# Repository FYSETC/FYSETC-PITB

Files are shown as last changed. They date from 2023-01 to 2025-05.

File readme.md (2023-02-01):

## FYSETC PITB

### 1. Product introduction

Thanks for the great effort of the PCB designers [DFH](https://github.com/deepfriedheroin), [Armchair-Engineering](https://github.com/Armchair-Engineering), [kageurufu](Https://GitHub.com/kageurufu) and the other members from community to make this come true.

### 2. Hardware guide

#### 2.1 pinout

<table>
   <tr><td>Features</td><td>PITB Pin</td><td>RP2040 Pin</td><td>Pin No.</td><td>Comment</td></tr>
   <tr><td rowspan="4">X-MOTOR(1)</td><td>X-Step</td><td>GPIO8</td><td>11</td><td></td></tr>
   <tr><td>X-DIR</td><td>GPIO7</td><td>9</td><td></td></tr>
   <tr><td>X-EN</td><td>GPIO5</td><td>7</td><td></td></tr>
   <tr><td>X-CS/PDN</td><td>GPIO6</td><td>8</td><td></td></tr>
   <tr><td rowspan="4">Y-MOTOR(2)</td><td>Y-Step</td><td>GPIO12</td><td>15</td><td></td></tr>
   <tr><td>Y-DIR</td><td>GPIO11</td><td>14</td><td></td></tr>
   <tr><td>Y-EN</td><td>GPIO9</td><td>12</td><td></td></tr>
   <tr><td>Y-CS/PDN</td><td>GPIO10</td><td>13</td><td></td></tr>
   <tr><td rowspan="3">TMC Driver SPI </td><td>MOSI</td><td>GPIO3</td><td>5</td><td></td></tr>
   <tr><td>MISO</td><td>GPIO0</td><td>2</td><td></td></tr>
   <tr><td>SCK</td><td>GPIO2</td><td>4</td><td></td></tr>
   <tr><td rowspan="2">End-stops</td><td>X-STOP</td><td>GPIO23</td><td>35</td><td>Jumper connection for X-DIAG</td></tr>
   <tr><td>Y-STOP</td><td>GPIO24</td><td>36</td><td>Jumper connection for Y-DIAG</td></tr>
   <tr><td rowspan="3">FAN/RGB</td><td>FAN0</td><td>GPIO20</td><td>31</td><td></td></tr>
   </td><td>FAN1</td><td>GPIO21</td><td>32</td><td></td></tr>
   </td><td>RGB</td><td>GPIO29</td><td>41</td><td></td></tr>
   <tr><td rowspan="1">Temperature</td><td>TE0（THERM0）</td><td>GPIO26</td><td>38</td><td>A 4.7kOhm 0.1% temperature sensor pull up resistor is used,PT1000 can be connected directly. For PT100, an amplifier board must be used.</td></tr>
   <tr><td rowspan="2">CAN</td><td>TX</td><td>GPIO13</td><td>16</td><td></td></tr>
   <tr><td>RX</td><td>GPIO14</td><td>17</td><td></td></tr>
   <tr><td rowspan="2">EEPROM I2C Pin-Out</td><td>SCL</td><td>GPIO17</td><td>28</td><td></td></tr>
   <tr><td>SDA</td><td>GPIO16</td><td>27</td><td></td></tr>
   <tr><td rowspan="3">SWD Debug</td><td>SWDIO</td><td>SWDIO</td><td>25</td><td>only used for debugging now and can be used for other purposes.</td></tr>
   <tr><td>SWCLK</td><td>SWCLK</td><td>24</td><td>only used for debugging now and can be used for other purposes.</td></tr>
   </td><td>RESET</td><td>#RUN</td><td>26</td><td></td></tr>
</table>

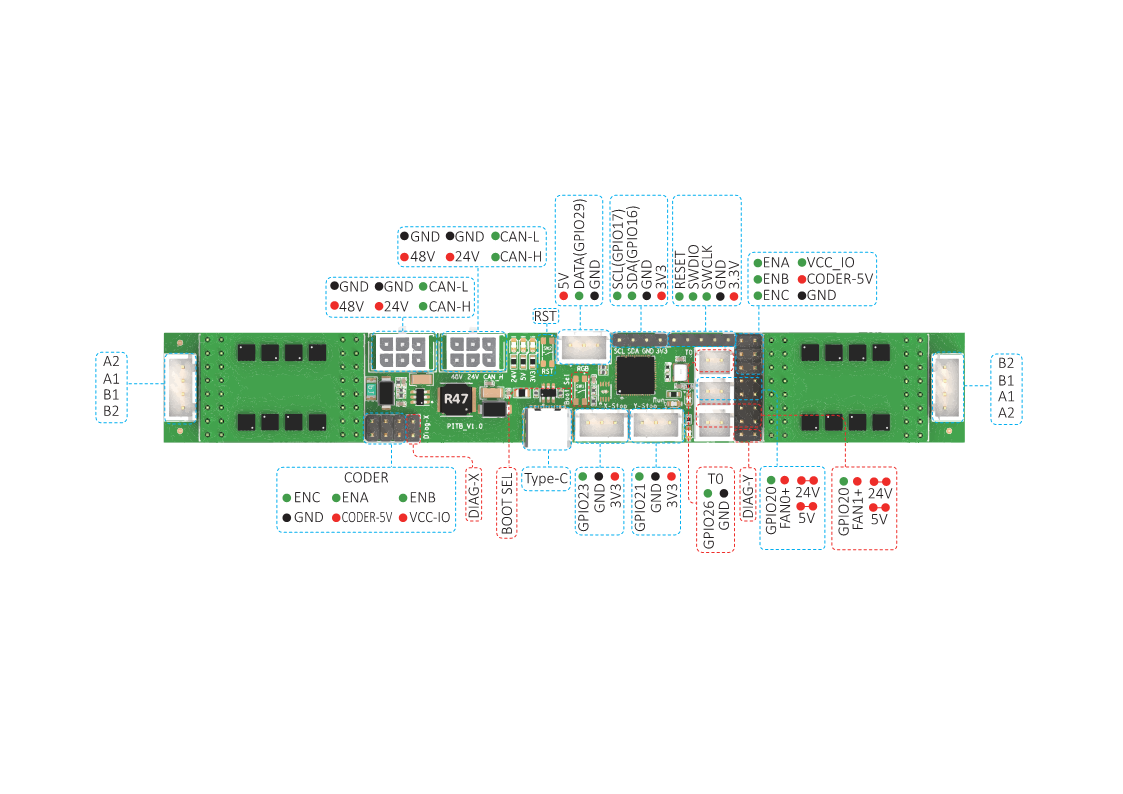
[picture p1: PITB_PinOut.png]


## Firmware

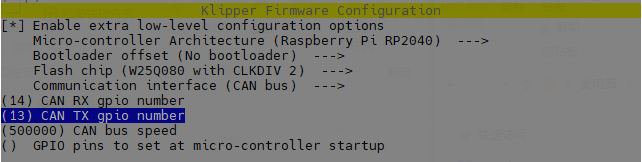
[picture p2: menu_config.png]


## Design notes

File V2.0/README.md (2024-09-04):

## PITB V2.0

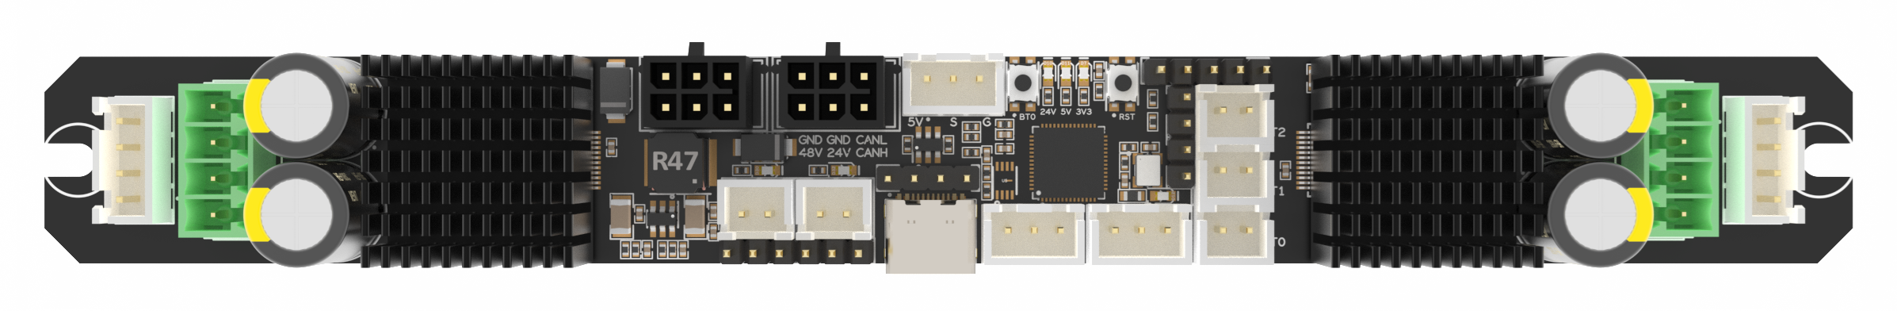
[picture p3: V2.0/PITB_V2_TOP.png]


### 1. Product introduction

Thanks for the great effort of the PCB designers [DFH](https://github.com/deepfriedheroin), [Armchair-Engineering](https://github.com/Armchair-Engineering), [kageurufu](Https://GitHub.com/kageurufu) and the other members from community to make this come true.

### 2. Hardware guide

#### 2.1 pinout

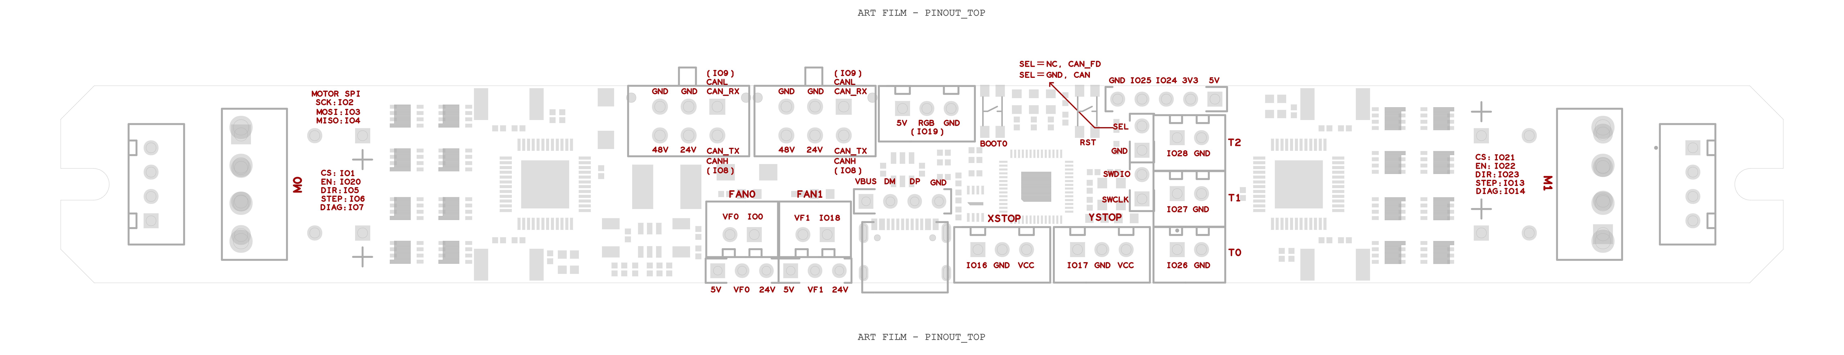
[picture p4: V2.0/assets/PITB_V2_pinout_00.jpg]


## Firmware

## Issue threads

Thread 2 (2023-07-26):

Unable to write tmc spi 'stepper_x' register GLOBALSCALER  HELPPP!!!

rbentoski2113, 2023-07-26:
I got the Fystec PITB with the 2 BIG 5160s can board, got it working on can and everything works, fans rgb  leds and whatnot but get this eror message when trying to move the x or y (what im using them on) steppers, googling has been of no help.   im still trying to rap my head around the spi/ ic2 bus and how it works, but has anyone else ran into this issue?

TekuSP, 2023-08-19:
You have to power 48V as well. Just jump 24V to both 48V and 24V rails.

rbentoski2113, 2023-08-19:
thank you! i thought i had updated this post i found this same coment somewhere like 20 mins after posting this orginaly.   If i may ask where did you find this out? cause there documentation is garbage

TekuSP, 2023-08-20:
By fucking around with wires until it started working.
At least now I can use thick 48V wires to transfer power to extruder CAN Board rather than thin 24 V wires...

ejhoness, 2024-08-31:
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

KoiosLabs, 2024-09-10:
Got the spi bus working: https://github.com/Klipper3d/klipper/pull/6683

ejhoness, 2024-09-20:
my pitbv2 is broken,

thanks, long life and prosperity.

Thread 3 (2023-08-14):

CODER pins not explained

TekuSP, 2023-08-14:
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
For what purpose are used those pins? What should be connected to them? ABZ from Encoder? Do they lead to ABN in TMC?

rbentoski2113, 2023-08-24:
i second this

> 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 For what purpose are used those pins? What should be connected to them? ABZ from Encoder? Do they lead to ABN in TMC?

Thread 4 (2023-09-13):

What model are the two 6-pin connectors for the CAN-BUS

abassign, 2023-09-13:
What model are the two 6-pin connectors for the CAN-BUS and voltages 24 and 48? Is it possible to find them on Amazon?

rbricheno, 2023-09-19:
I have one of these boards in hand and measured the connectors to work this out.

They are  "43025-0600" 6 circuit Micro-fit 3.0 connectors as described here: https://www.utmel.com/components/43025-0800-micro-fit-3-0-receptacle-housing-dual-row-drawing-datasheet-and-equivalents?id=1277

I took a photograph of the board next to some calipers which you can see here:  https://imgur.com/a/ZejbaVU

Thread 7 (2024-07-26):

PIN description for V2 is just a copy of that for V1. Couod you please correct it? Thanks.

salbang, 2024-07-26:

eddwatts, 2024-07-27:
been working on this myself and have put in a pull request to it, pinouts, sample cfg and firmware details for klipper
[https://github.com/eddwatts/FYSETC-PITB/tree/main/V2.0](https://github.com/eddwatts/FYSETC-PITB/tree/main/V2.0
)
Only bit untested are the SPI ports as im not sure there working on my board, everything else is right and according to the schematics they should work so please try and give feedback

salbang, 2024-07-28:
@eddwatts Thanks. Will try it once I get the v2 one delivered.

ejhoness, 2024-08-31:
for me, at the moment, spi errors, tmc dump only ffffffffff, and not working fan0 fan1 temp port012 ok and sensor GPIO29_ADC3 ok
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

:(

KoiosLabs, 2024-09-10:
Got the spi bus working: https://github.com/Klipper3d/klipper/pull/6683

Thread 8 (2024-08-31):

support PITbv2

ejhoness, 2024-08-31:
I'm sad about this, please show me a video of this working with klipper. A simple motor rotating connected to this. PITBv2. and the files used to run this motor.

ejhoness, 2024-09-06:
Thanks for the update, but only temperature and end of stroke sensor. No motor and fans

[klippy_pitbv2.log](https://github.com/user-attachments/files/16910681/klippy_pitbv2.log)
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

KoiosLabs, 2024-09-10:
Got the spi bus working: https://github.com/Klipper3d/klipper/pull/6683

ejhoness, 2024-09-20:
my pitbv2 is broken,
thanks, long life and prosperity.

Closed 2024-09-20.

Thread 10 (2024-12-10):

PITB board not recognized by CAN network, tool head board in passthrough works fine.

LadPack, 2024-12-10:
I am trying and failing to have the Party in the back (PITB) board recognized.

I know the CAN wiring is correct, because I have it daisy chained with a toolhead board (downstream of the PITB) that is running fine on klipper, it's just the PITB board that isn't running

I'm using these settings https://github.com/kageurufu/PITB/tree/main/firmware
I am able to see the board over USB, but once I put it into the CAN network I see just the toolhead board like below.

I have also double triple checked the wiring on the board and made sure it is getting the appropriate power.

I am following esotericals guide online, including all of the steps for troubleshooting no UUID, I have reinstalled the katapult software multiple times, each time it appears to install normally.

FWIW, I did have to take down the CAN network and then bring it back up with 1m and qlen 1024, and that worked for the toolhead board (ebb36) that I was able to successfully install klipper on.

I have also removed the ebb36 from the loop, and am now just trying to flash the PITB on it's own. I have also tried with and without the CAN FD Jumper

LadPack, 2024-12-11:
closing, pins were incorrectly labelled on pictures

NAPCAL, 2025-03-19:
Your issue might just be this https://github.com/FYSETC/FYSETC-PITB/issues/11

NAPCAL, 2025-03-19:
The V1.0 has the identical CAN bus termination resistors installed, so your issue is the same as the V2.0. The PITB can only be used as an end of the bus device since termination has to be at the ends of the bus. https://github.com/FYSETC/FYSETC-PITB/issues/11

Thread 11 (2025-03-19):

PITB V2 bad CAN bus design with pass through connector with on-board bus termination (R28 & R29)

NAPCAL, 2025-03-19:
With R28 & R29 installed and no jumpers to disconnect them from the CAN bus, this board will only work as an end of the CAN bus device, and the additional connector is only suitable for passing power onto other devices.

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

Currently, these two resistors are tiny SMD; it will be almost impossible for a hobbyist to remove them without damaging the board.

I wanted to use the pass-through connector to supply the +24V, GND, CAN_L, & CAN_H onto my BTT SB2240 tool headboard, with it being the last device on the bus.

Jawfish1024, 2025-03-20:
I was able to use the flash the PITB as a USB can bus bridge to control my EBB 42 and Cartographer so it is the 1st device on the bus.
I still had to connect the board via USB from my Pi though

erdoganguner2004-code, 2025-09-05:
So, in order to use the second port for pass-through, is the solution as simple as removing the resistor?

NAPCAL, 2025-09-05:
Yes, both resistors are the most miniature SMD resistors I have seen.

Kapton tape to protect the other parts around the resistors, a heat gun (like Weller 6966C) or SMD rework gun, and a very small set of tweezers.

Weller 6966C is a very old product and maybe discontinued, but it keeps working and working.

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

NAPCAL, 2025-09-06:
CAN bus has very specific physical layer requirements to prevent noise and ringing during communications.

Bench setups (Bench testing) typically will not recreate bus wires running past wiring that can induce noise into the bus, nor will they recreate the movement of the bus wires for tool head boards.

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

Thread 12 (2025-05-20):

Homing wrong direction.

raschinger, 2025-05-20:
The default config file is nearly unusable. Therefore I used the fork from eddwatts. But still unusable. Could you please double check the pinout and so on?

It basically homed in the wrong direction. Steppers movement aren't invented confirmed it with force move in positiv direction.

https://github.com/user-attachments/assets/319c0959-71ea-45f4-a731-72db970b7530

[stepper_x]
step_pin = PITB:gpio6
dir_pin = !PITB:gpio5
enable_pin = !PITB:gpio20
endstop_pin = tmc5160_stepper_x:virtual_endstop
homing_retract_dist = 20
rotation_distance = 40
position_min = 0
position_endstop = 250
position_max = 250
homing_positive_dir = true
homing_speed = 150.0
second_homing_speed = 10.0
microsteps = 32

[tmc5160 stepper_x]
spi_bus = spi0_gpio4_gpio3_gpio2
cs_pin = PITB:gpio1
diag1_pin = PITB:gpio7
driver_sgt = -64
interpolate = False
run_current = 1

[stepper_y]
step_pin = PITB:gpio13
dir_pin = !PITB:gpio23
enable_pin = !PITB:gpio22
endstop_pin = tmc5160_stepper_y:virtual_endstop
homing_retract_dist = 20
rotation_distance = 40
position_min = 0
position_endstop = 250
position_max = 250
homing_positive_dir = true
homing_speed = 150.0
second_homing_speed = 10.0
microsteps = 32

[tmc5160 stepper_y]
spi_bus = spi0_gpio4_gpio3_gpio2
cs_pin = PITB:gpio21
diag1_pin = PITB:gpio14
driver_sgt = -64
interpolate = False
run_current = 1

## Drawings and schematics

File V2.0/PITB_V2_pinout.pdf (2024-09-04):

# ART FILM - PINOUT_TOP

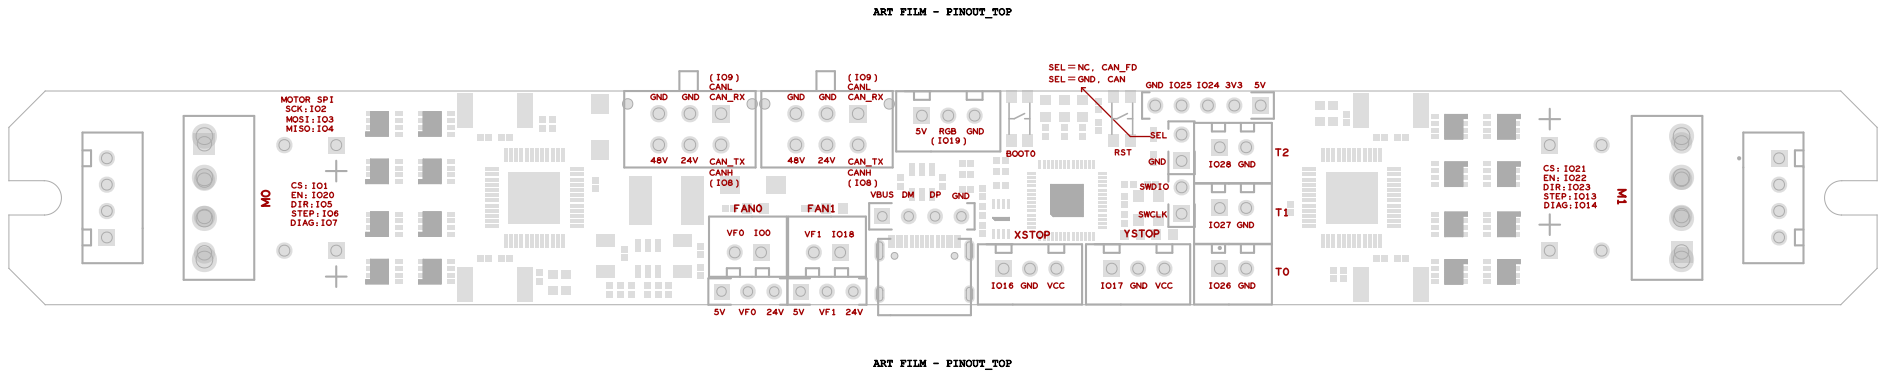
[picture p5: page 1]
ART FILM - PINOUT_TOP; SCK:IO2; MISO:IO4; MOSI:IO3; MOTOR SPI; DIAG:IO7; STEP:; DIR:; GND; CANH; CAN_TX; CANL; CAN_RX; FAN0; FAN1; VBUS; RGB; XSTOP; BOOT0; VCC; RST; YSTOP; SWCLK; SWDIO; SEL; DIAG:IO14; STEP:IO13

SEL NC, CAN_FD
SEL GND, CAN

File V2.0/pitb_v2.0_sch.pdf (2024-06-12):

5

4

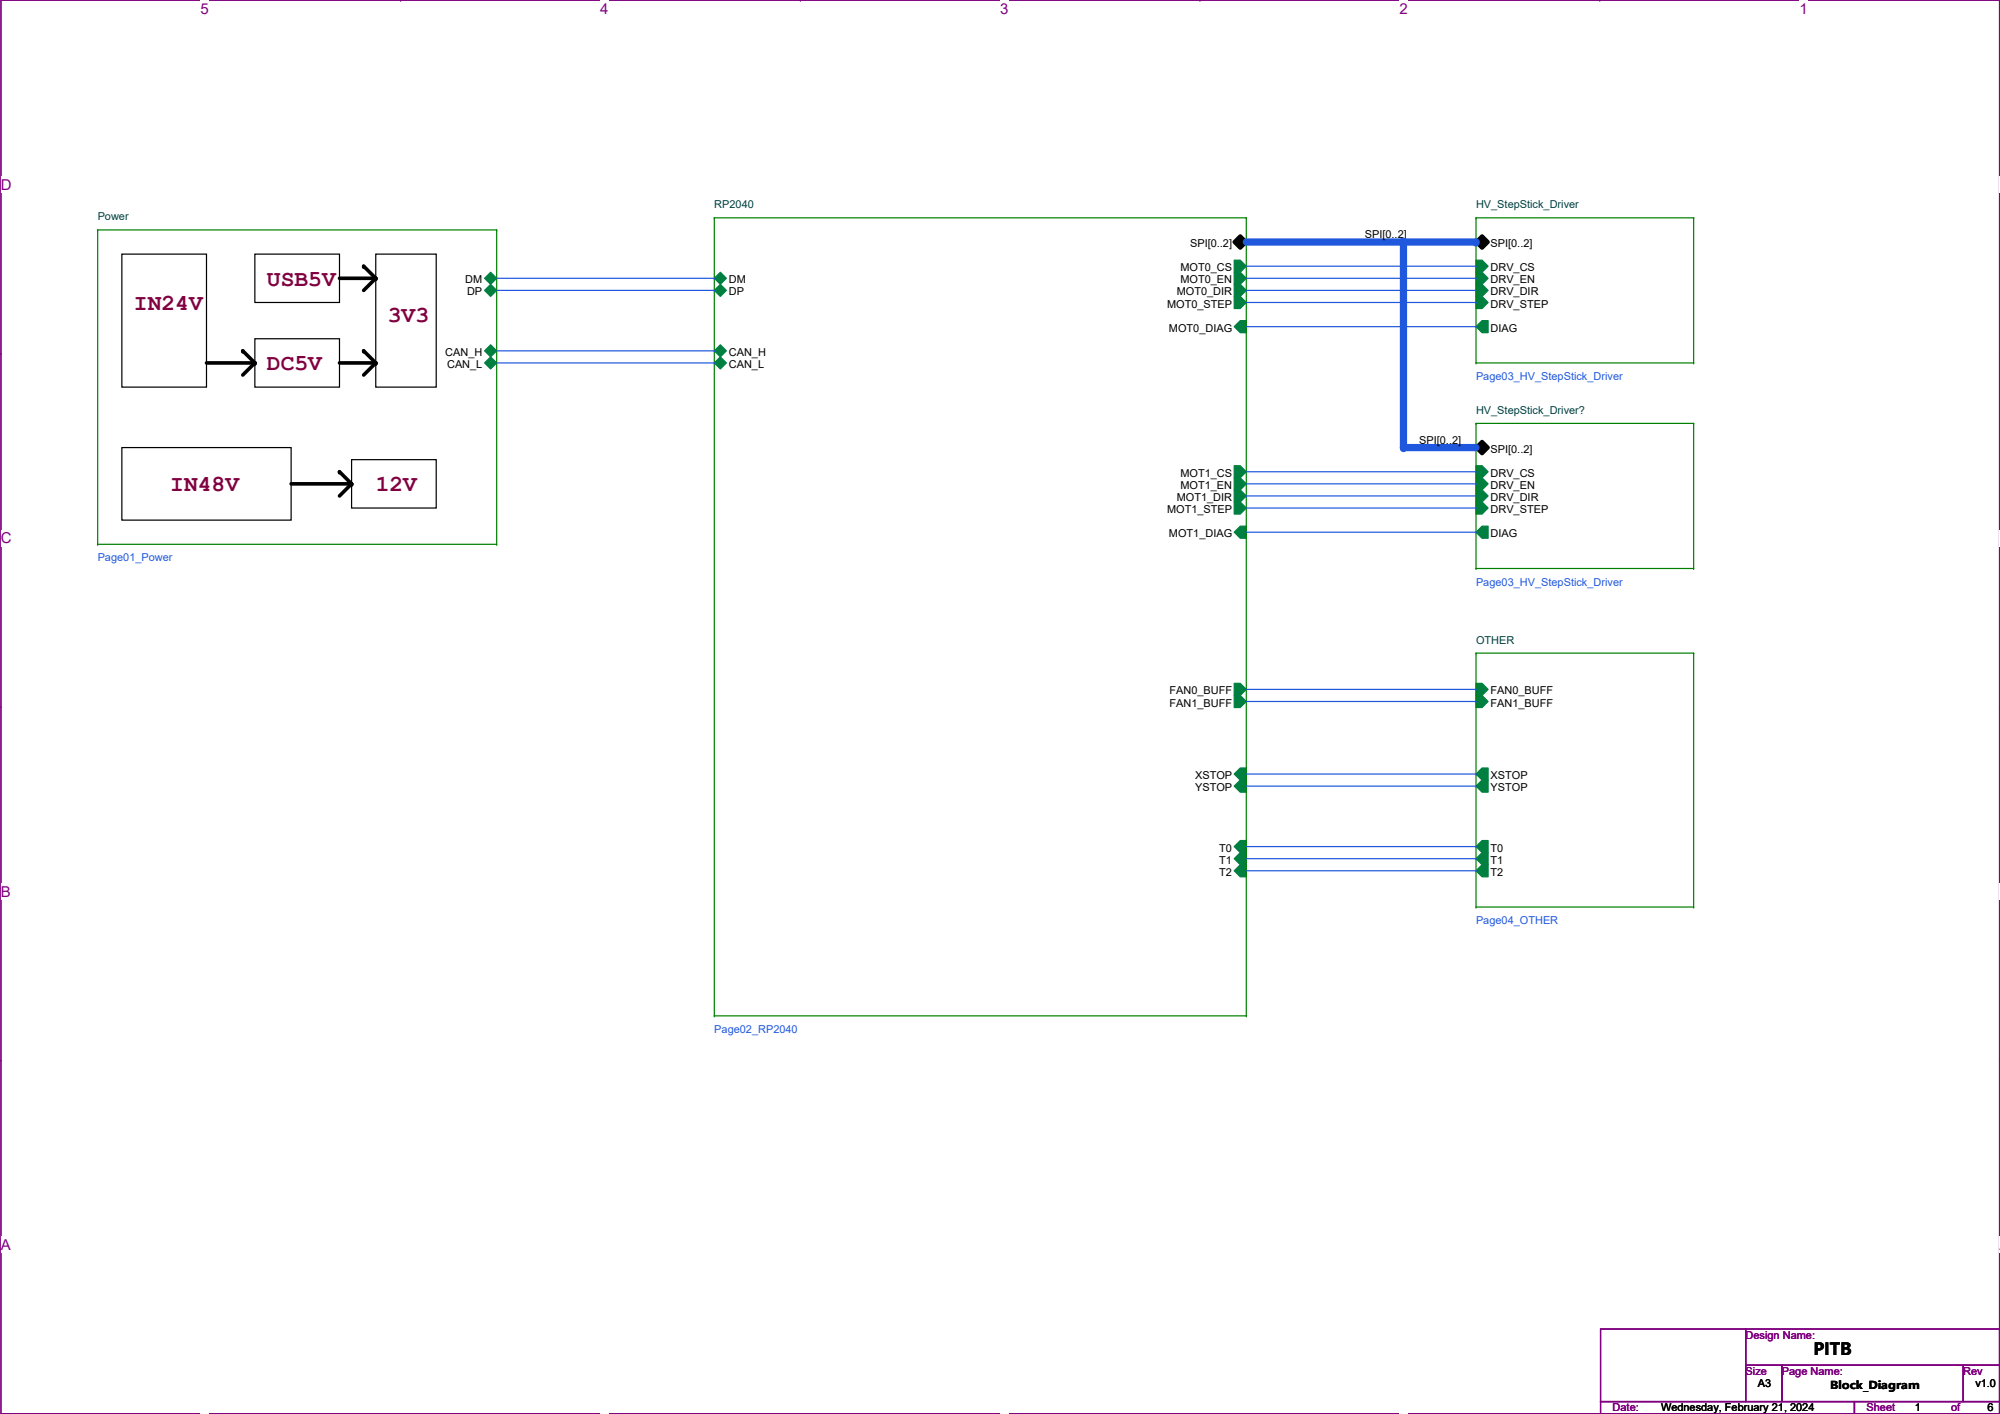
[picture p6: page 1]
USB5V; Design Name:; Size; Page Name:; Rev; Date:; Sheet; PITB; Wednesday, February 21, 2024; Block_Diagram; Page02_RP2040; MOT1_EN; FAN0_BUFF FAN1_BUFF; SPI[0..2]; MOT1_CS; MOT1_DIR MOT1_STEP; CAN_H CAN_L; YSTOP; XSTOP; MOT0_DIR; MOT0_EN; MOT0_DIAG; MOT0_STEP; MOT0_CS; MOT1_DIAG; HV_StepStick_Driver?; Page03_HV_StepStick_Driver; DIAG; DRV_DIR; DRV_EN; DRV_STEP; DRV_CS; HV_StepStick_Driver; OTHER; Page04_OTHER; XSTOP YSTOP; Power; Page01_Power

D D

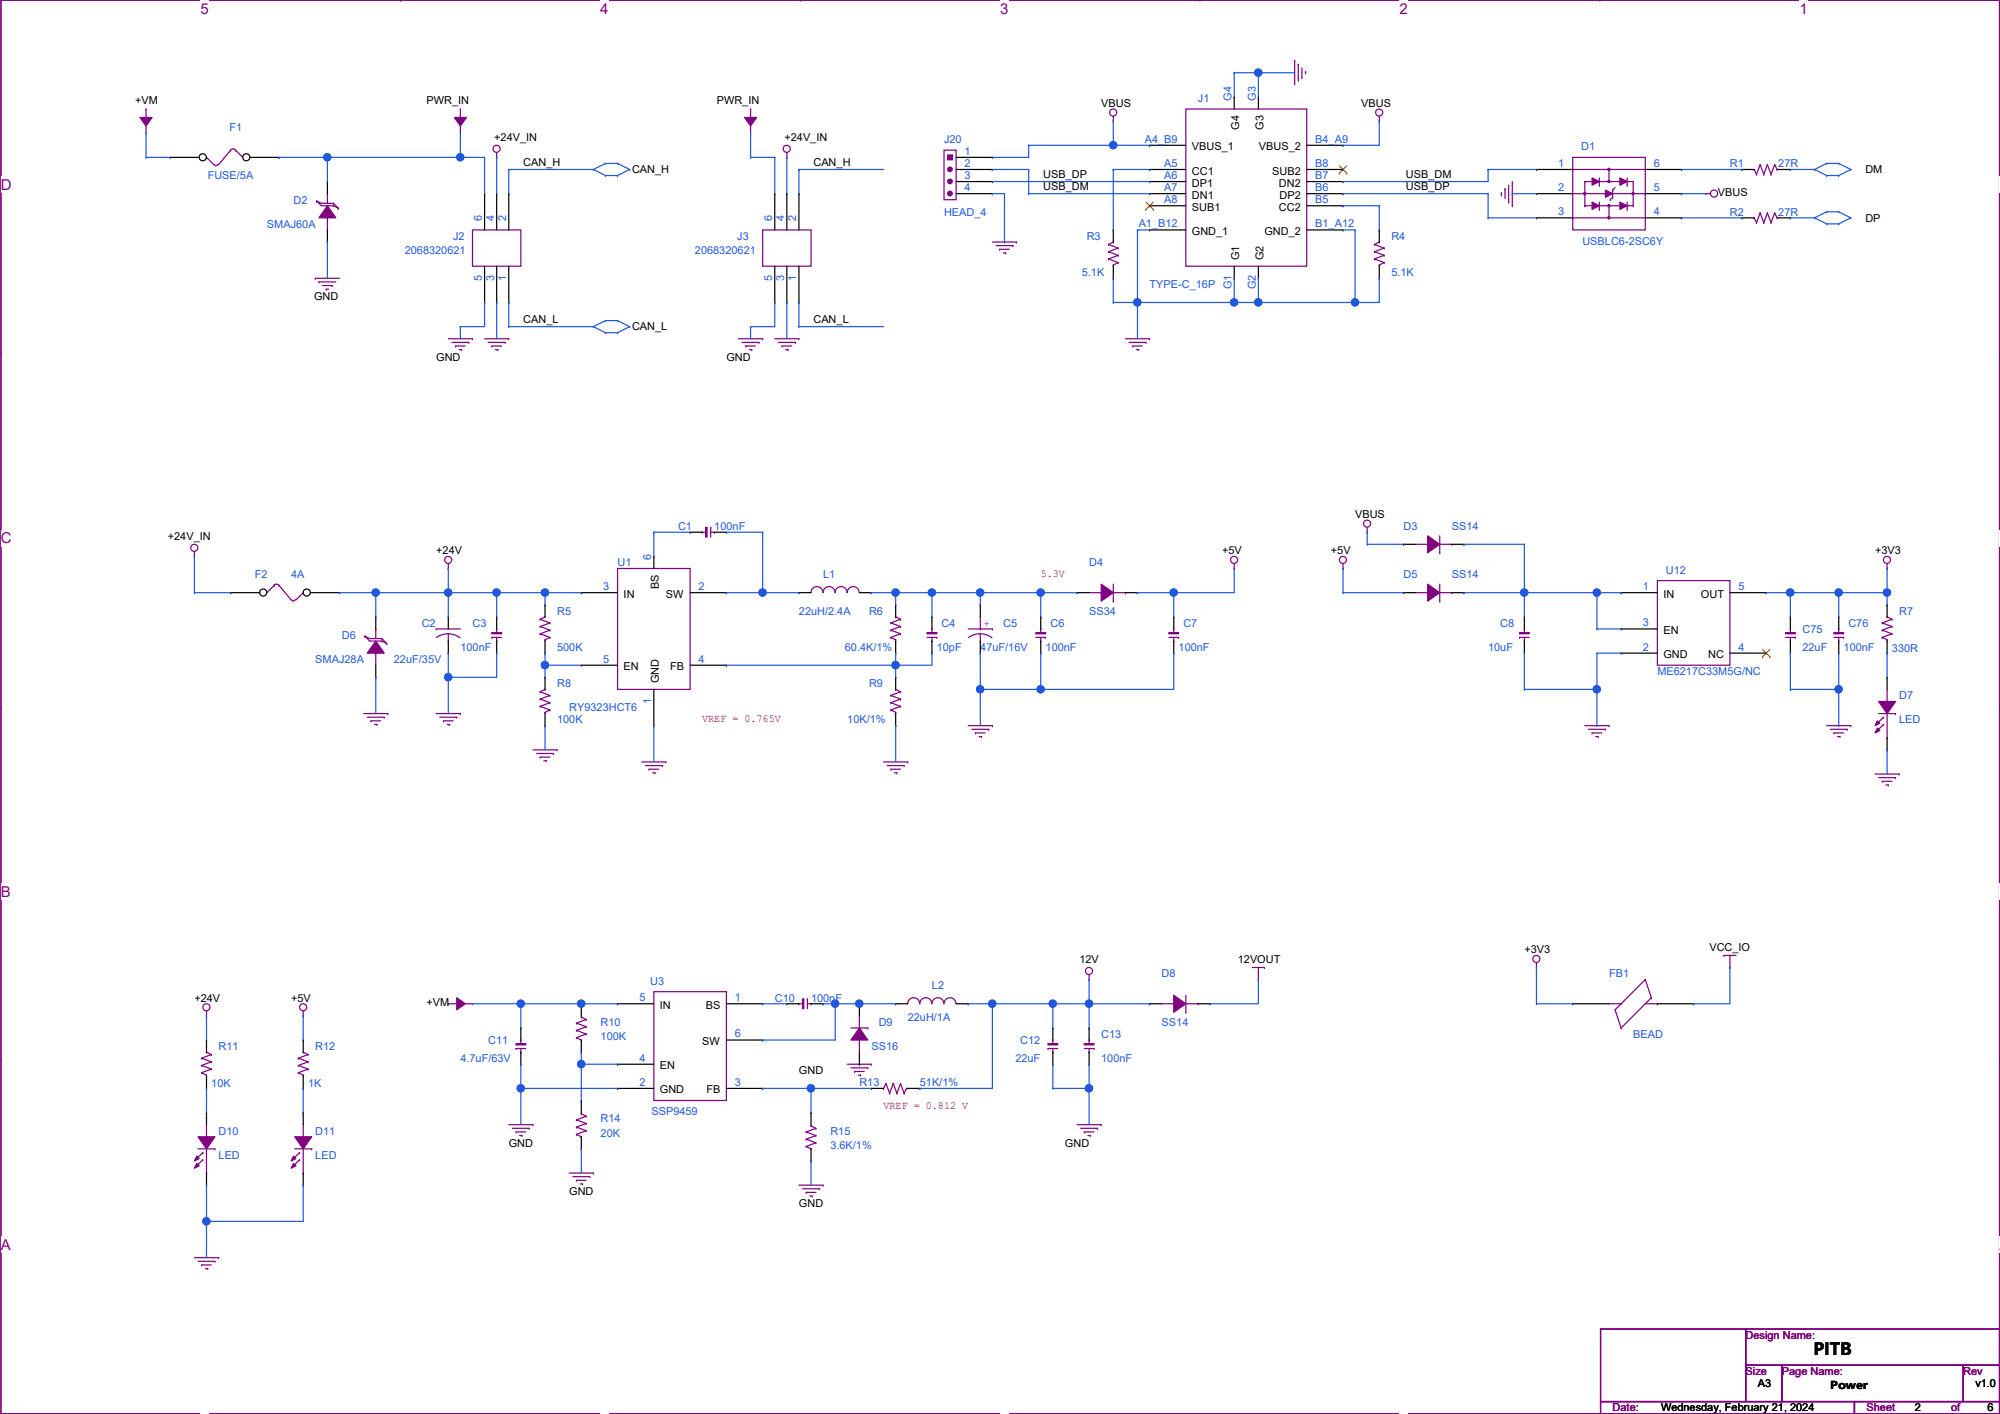
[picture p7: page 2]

D D

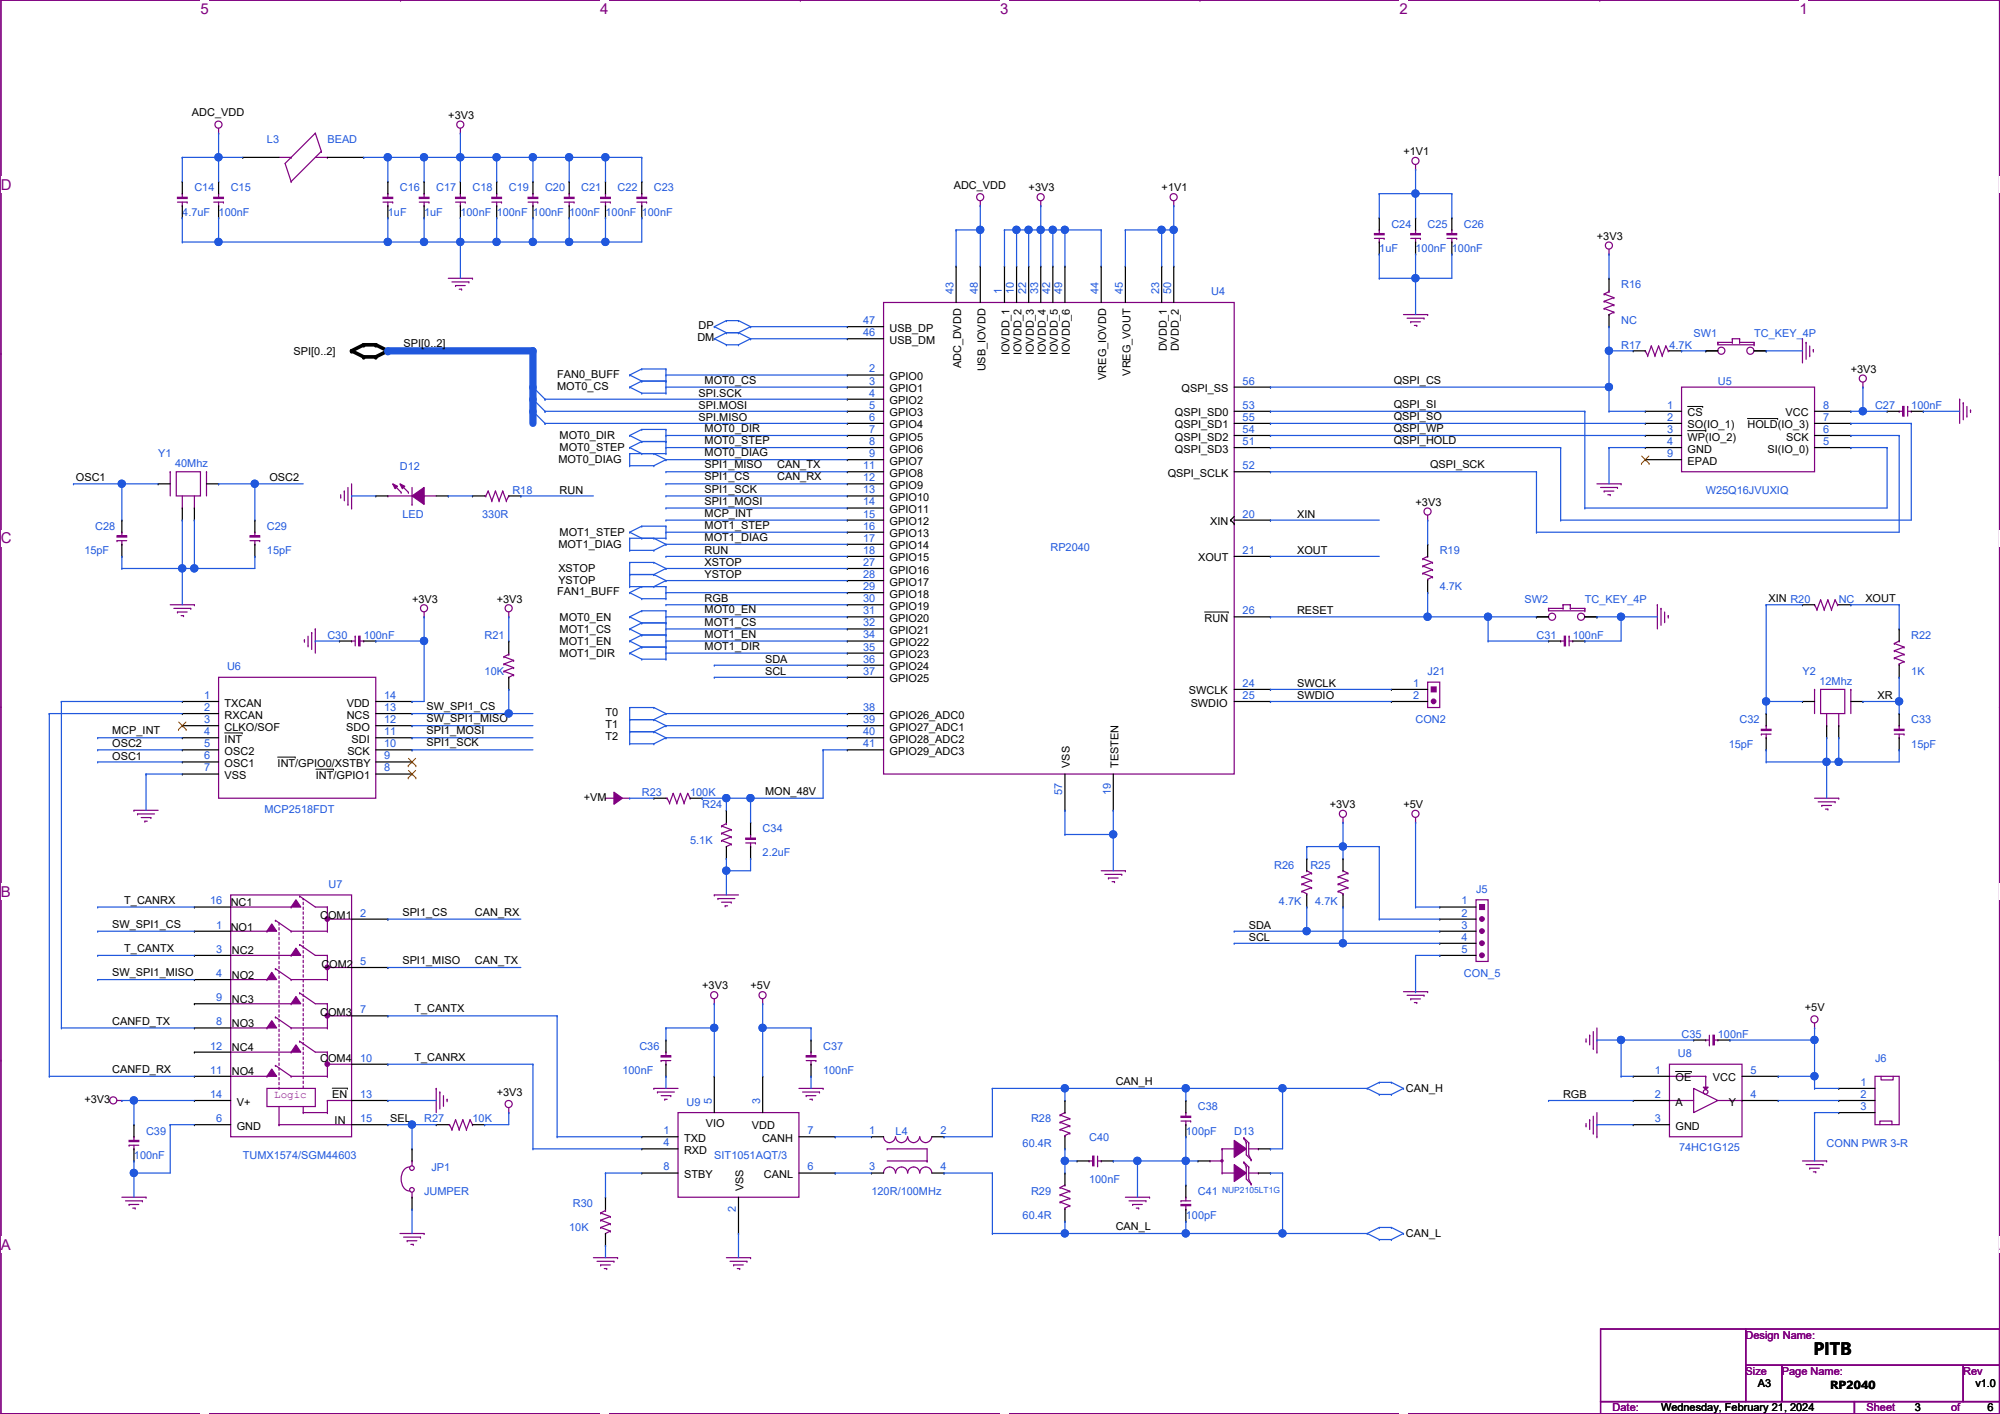
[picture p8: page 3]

D D

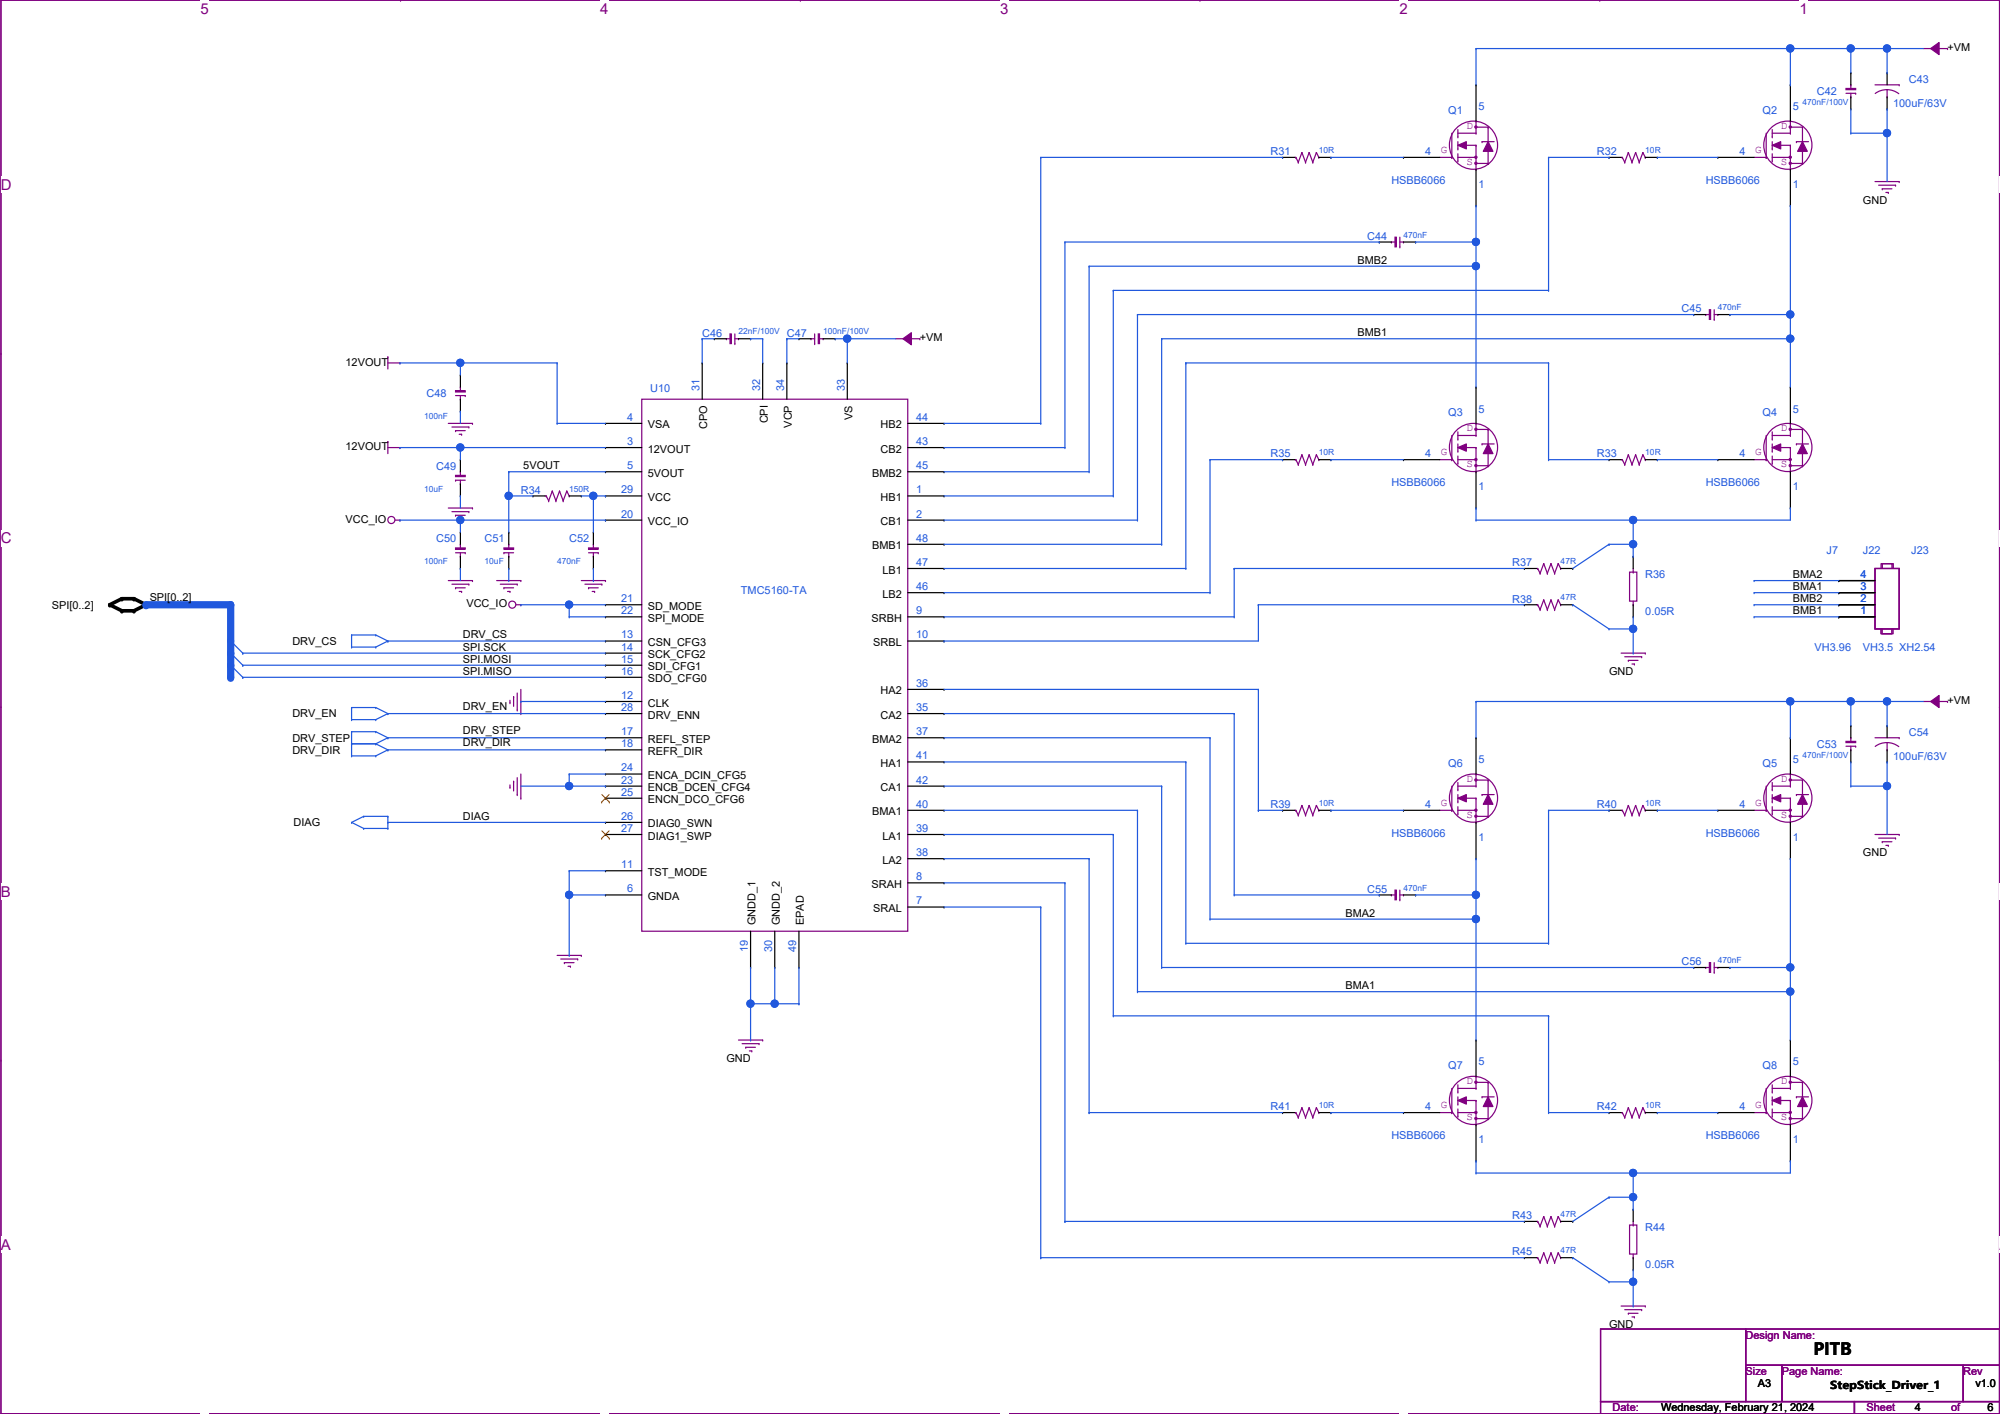
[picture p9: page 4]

D D

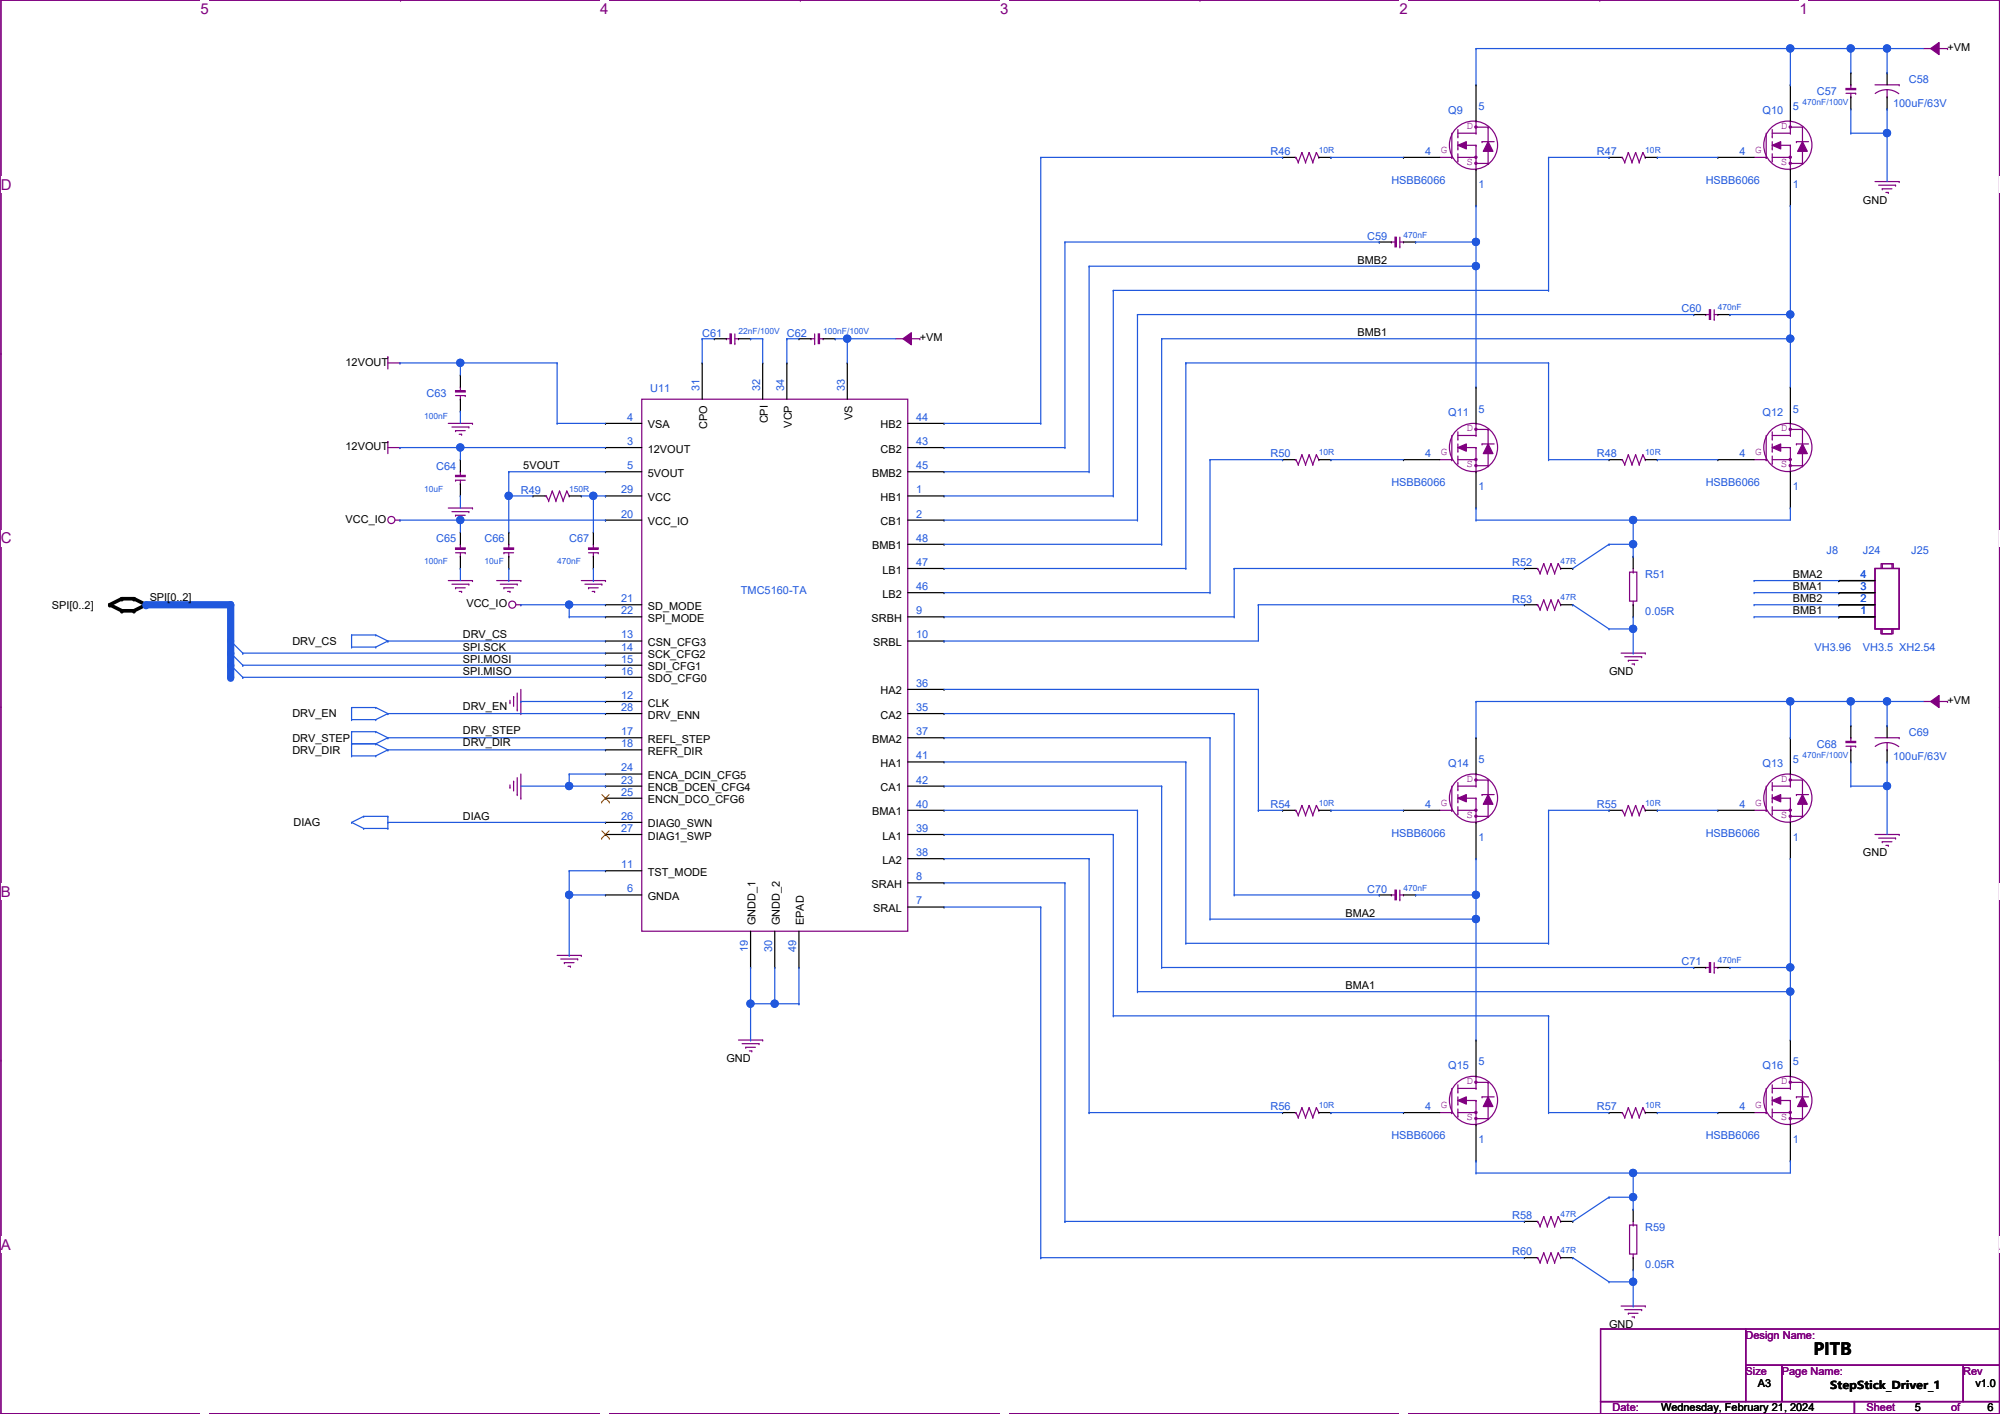
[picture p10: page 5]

D D

# Fan

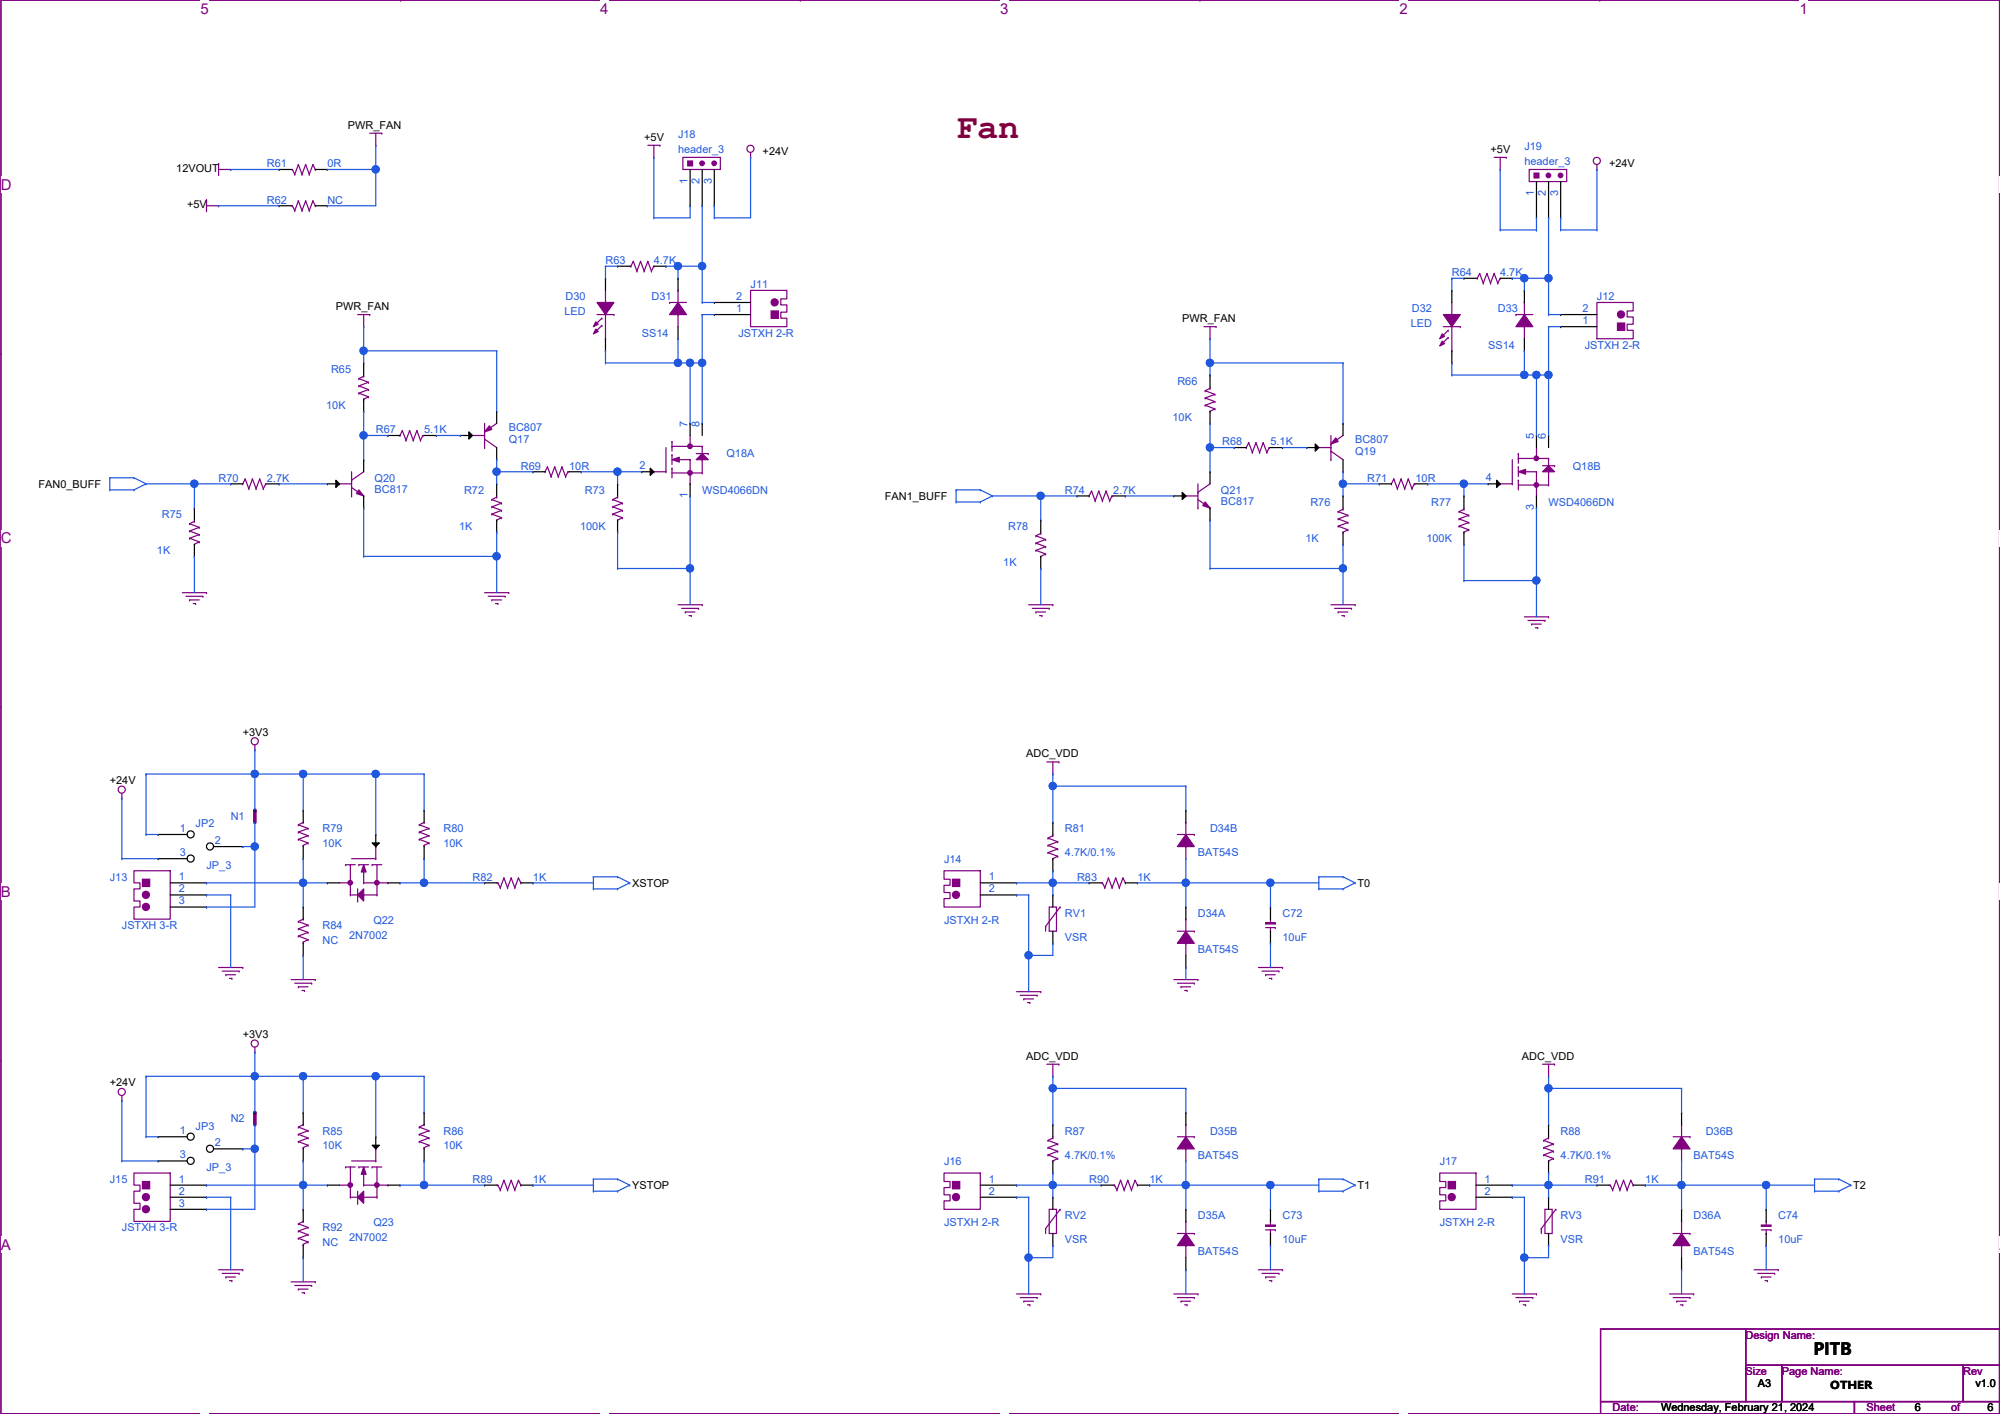
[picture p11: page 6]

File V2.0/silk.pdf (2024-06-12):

# ART FILM - adt

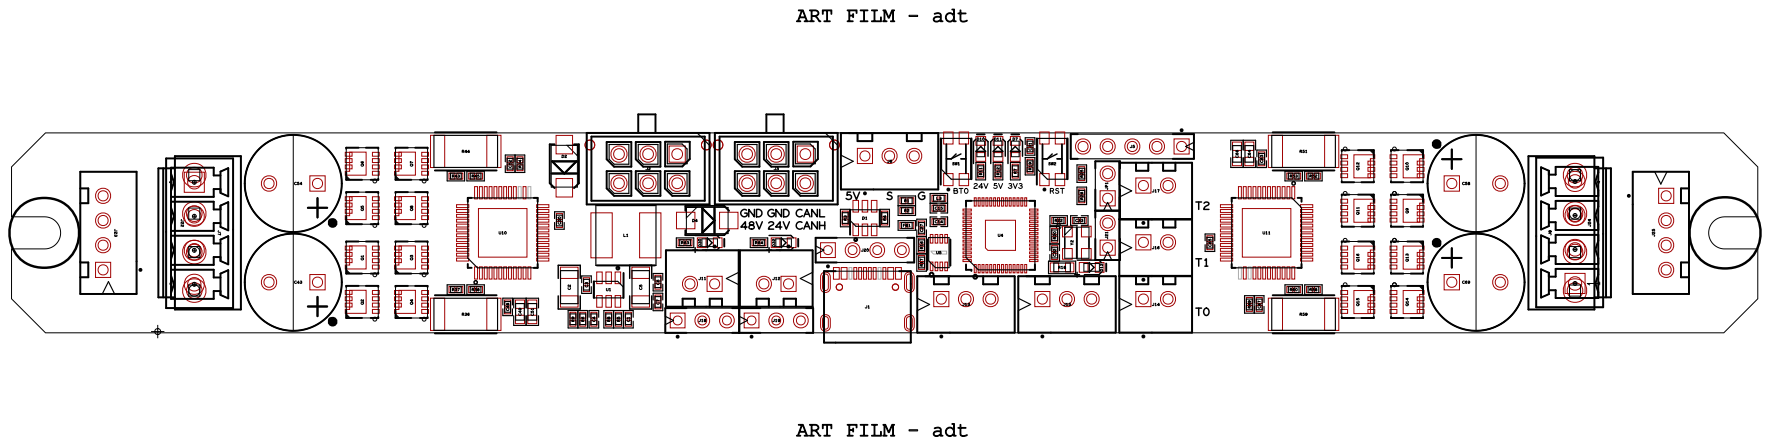
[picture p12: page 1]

# ART FILM - adb

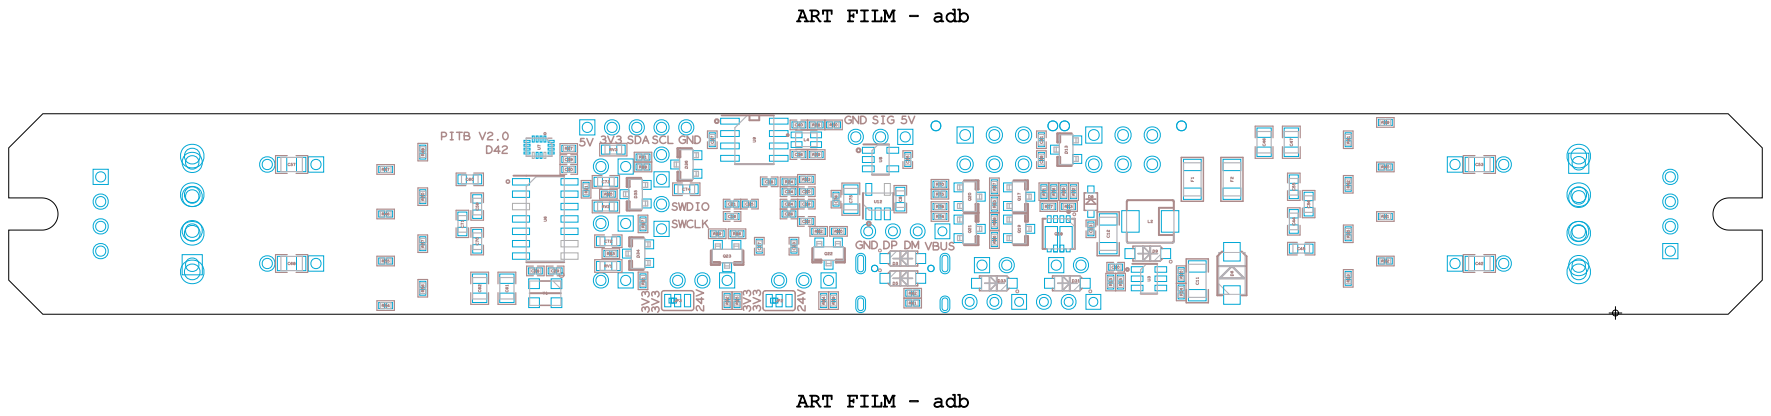
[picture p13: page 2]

# ART FILM - silktop

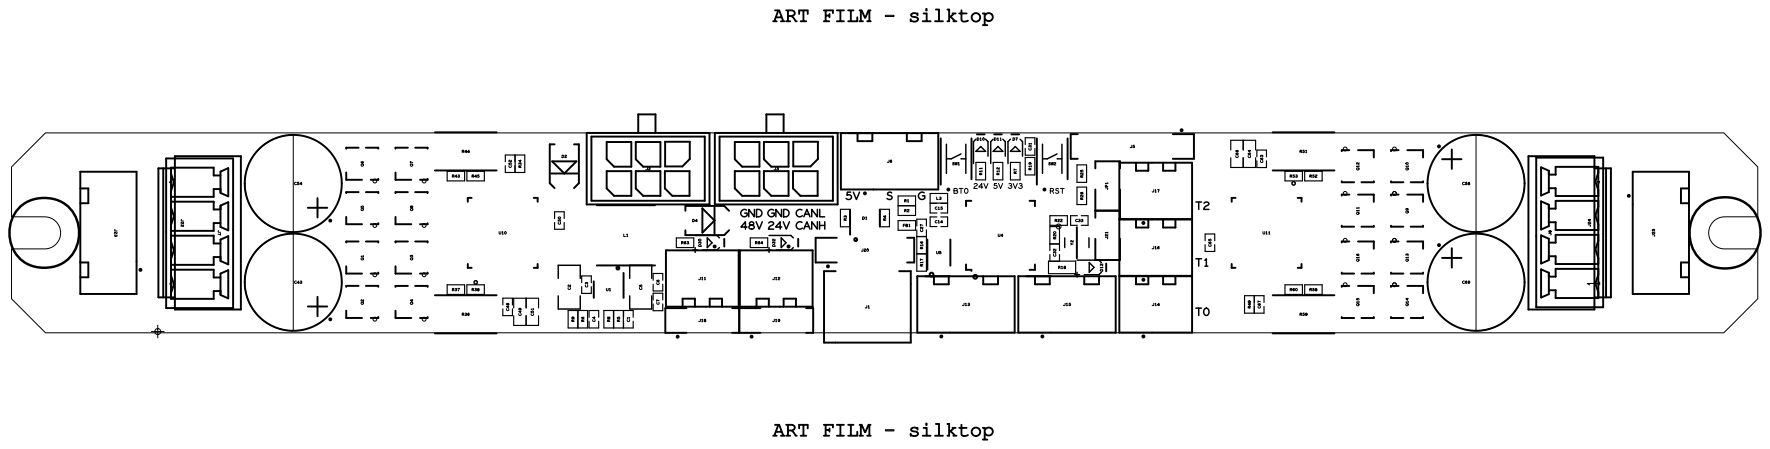
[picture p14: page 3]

# ART FILM - silkbotm

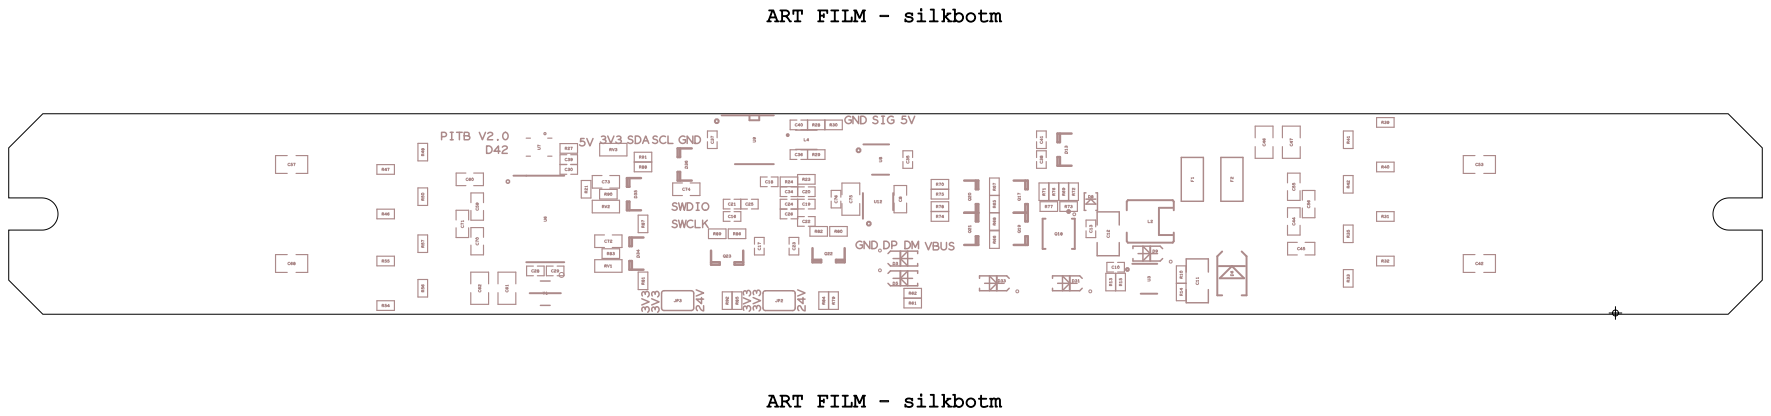
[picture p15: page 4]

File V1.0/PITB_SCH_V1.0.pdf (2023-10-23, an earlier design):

### IN24V

### USB5V

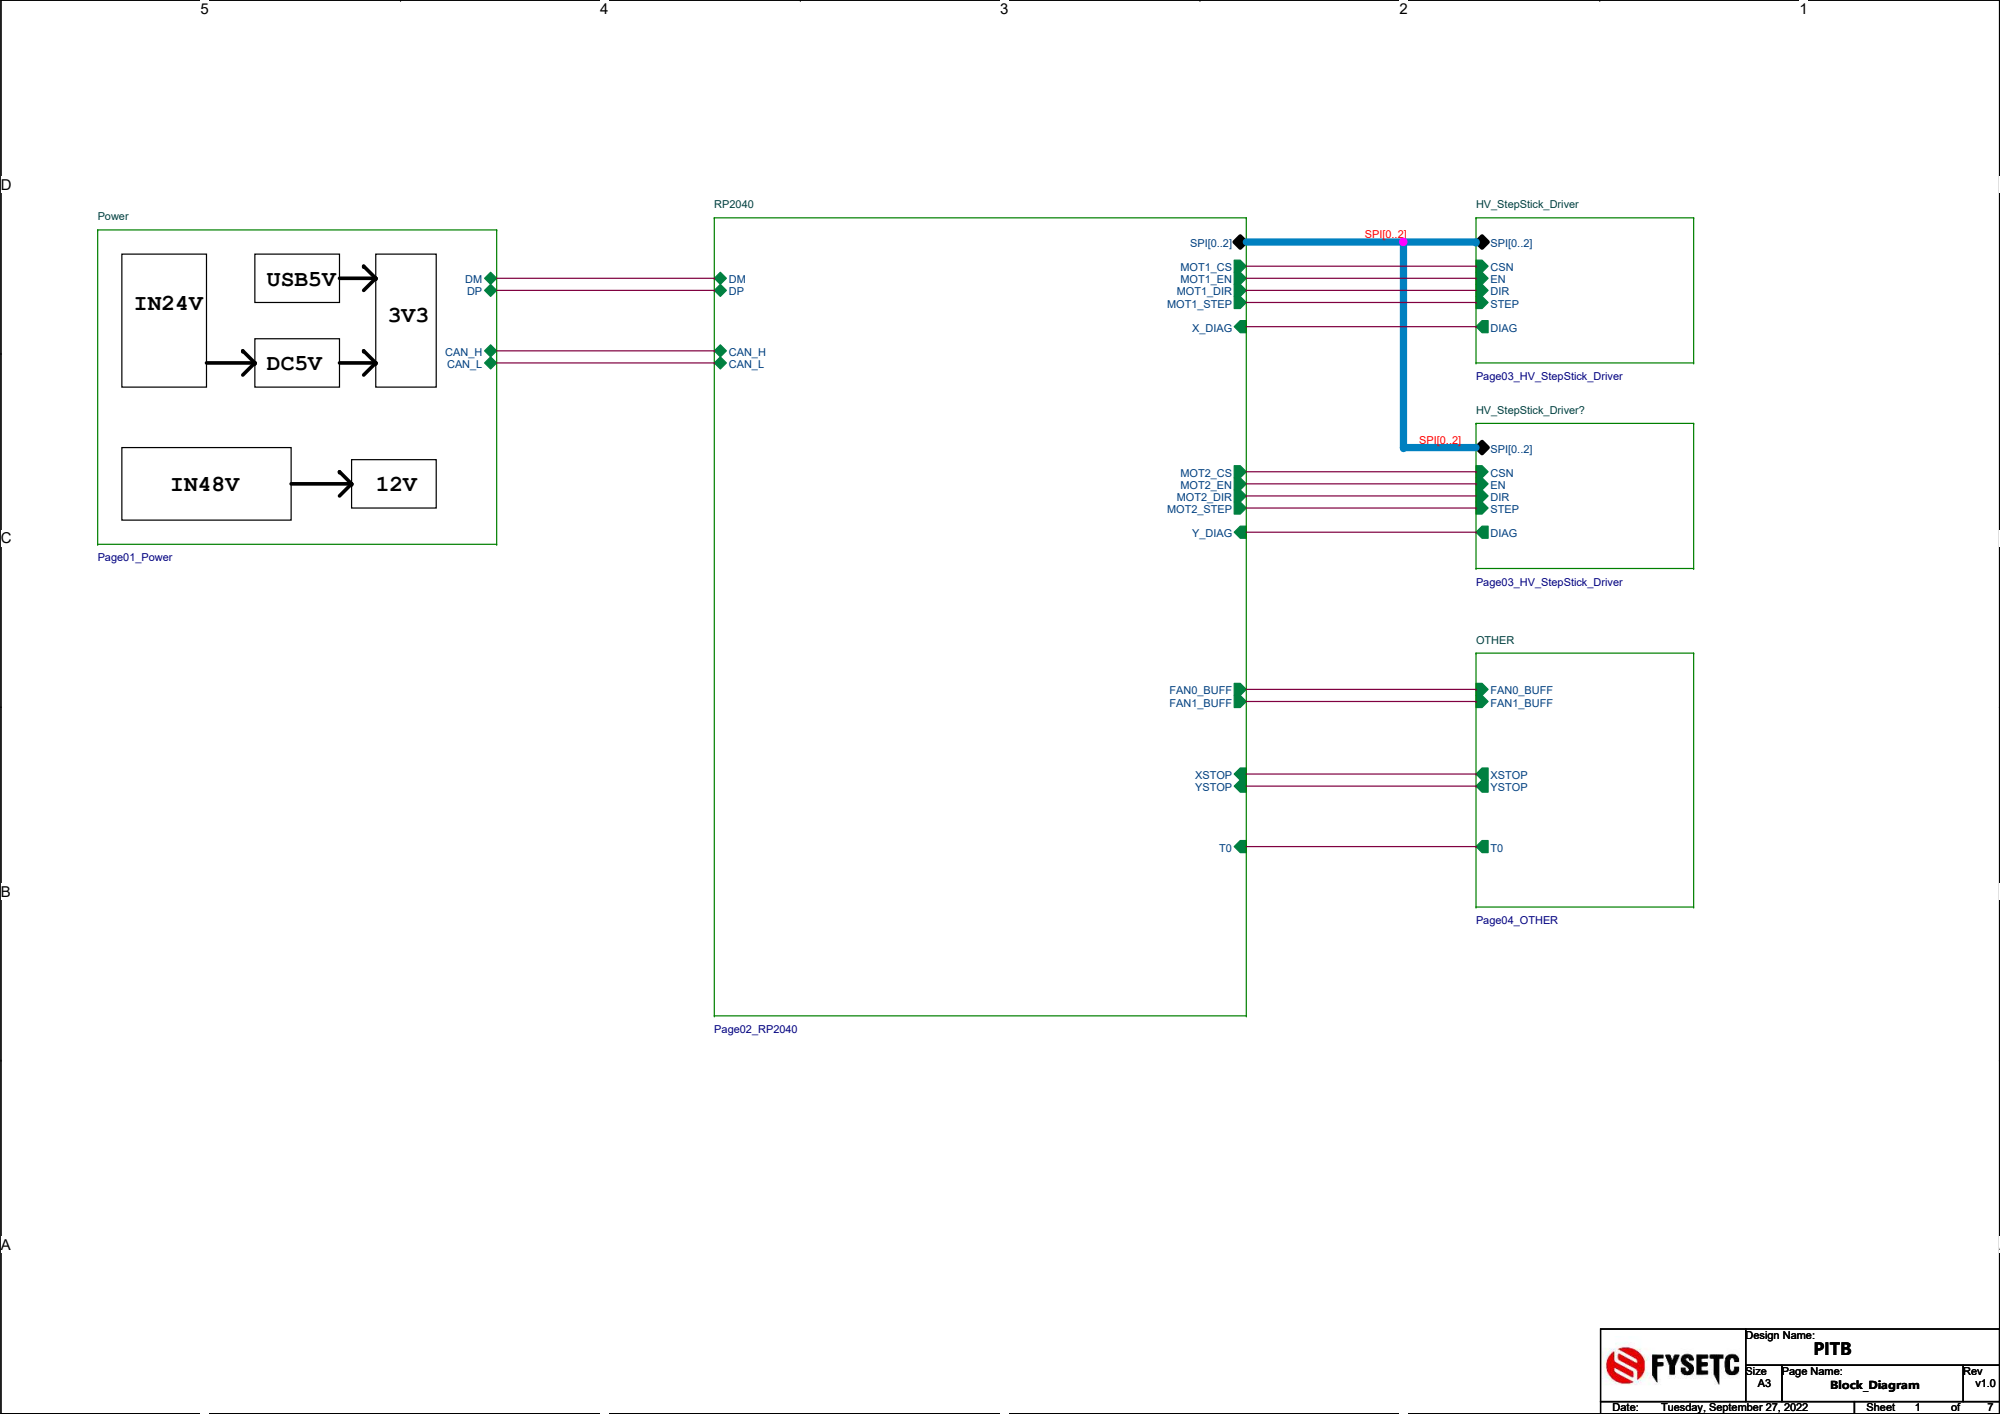
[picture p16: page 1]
Design Name:; Size; Page Name:; Rev; Date:; Sheet; PITB; Tuesday, September 27, 2022; Block_Diagram; Page02_RP2040; MOT1_EN; FAN0_BUFF FAN1_BUFF; SPI[0..2]; MOT1_CS; MOT1_DIR MOT1_STEP; MOT2_EN; MOT2_CS; MOT2_DIR MOT2_STEP; CAN_H CAN_L; X_DIAG; YSTOP; XSTOP; Y_DIAG; HV_StepStick_Driver?; Page03_HV_StepStick_Driver; CSN; DIR STEP; DIAG; HV_StepStick_Driver; OTHER; Page04_OTHER; XSTOP YSTOP; Power; Page01_Power

5 | 4 | 3 | 2 | 1

D


PAGE1 PAGE1 PAGE1

Wednesday, September 14, 2022 Wednesday, September 14, 2022 Wednesday, September 14, 2022 | 2 2 2 7 7 7

D


Power Power Power

Wednesday, September 14, 2022 Wednesday, September 14, 2022 Wednesday, September 14, 2022 | 3 3 3 7 7 7

D


QSPI_SO | SO(IO_1) 2
QSPI_WP | WP(IO_2) 3

Wednesday, September 14, 2022 Wednesday, September 14, 2022 Wednesday, September 14, 2022 | 4 4 4 7 7 7

D


StepStick_Driver_1 StepStick_Driver_1 StepStick_Driver_1

Wednesday, September 14, 2022 Wednesday, September 14, 2022 Wednesday, September 14, 2022 | 5 5 5 7 7 7

D


StepStick_Driver_1 StepStick_Driver_1 StepStick_Driver_1

Wednesday, September 14, 2022 Wednesday, September 14, 2022 Wednesday, September 14, 2022 | 6 6 6 7 7 7

D

# Fan


OTHER OTHER OTHER

Wednesday, September 14, 2022 Wednesday, September 14, 2022 Wednesday, September 14, 2022 | 7 7 7

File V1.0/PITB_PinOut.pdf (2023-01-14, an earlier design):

CAN-H; GND CODER-5V; ENC ENA; DIAG-X; ENB; GPIO20 FAN0+; VCC-IO; RST; BOOT SEL; ENA ENB ENC; VCC_IO CODER-5V GND; GPIO26; GND; DATA(GPIO29); SCL(GPIO17); SDA(GPIO16); GND 3V3; RESET; SWDIO SWCLK GND 3.3V; Type-C; GPIO23; GPIO21; CODER; DIAG-Y; GPIO20; FAN1+24V 5V

GND GND CAN-L

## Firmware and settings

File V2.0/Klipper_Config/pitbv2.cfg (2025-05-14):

[mcu PITB]
##  You need to select 'Communication interface' to USB in 'make menuconfig'
##  when you compile Klipper
##	Obtain definition by "ls -l /dev/serial/by-id/" then unplug to verify
##--------------------------------------------------------------------
#serial: /dev/serial/by-id/usb-Klipper_rp2040_E66160F423669A37-if00
canbus_uuid=e3cfde1a684f
## When using klipper with PITB V2, you can only use CAN or USB. When using CAN, 
## you need to short-circuit SEL and GND, that is, plug in the jumper cap.
## Uncomment below if you're using the Raspberry uart0 to communicate with Spider
#restart_method: command

#####################################################################
#      X/Y Stepper Settings
#####################################################################

[stepper_x]
##	Connected to MOT0 (B Motor)
step_pin: PITB:gpio6
dir_pin: PITB:gpio5
enable_pin: !PITB:gpio20
rotation_distance: 40
microsteps: 16
full_steps_per_rotation:200  #set to 400 for 0.9 degree stepper
endstop_pin: ^PITB:gpio16
position_min: 0

##--------------------------------------------------------------------

##	Uncomment below for 250mm build
#position_endstop: 250
#position_max: 250

##	Uncomment for 300mm build
position_endstop: 300
position_max: 300

##	Uncomment for 350mm build
#position_endstop: 350
#position_max: 350

##--------------------------------------------------------------------
homing_speed: 25   #Max 100
homing_retract_dist: 5
homing_positive_dir: true

##  Make sure to update below for your relevant driver (5160)
[tmc5160 stepper_x]
## Soft SPI
spi_software_sclk_pin: PITB:gpio2
spi_software_mosi_pin: PITB:gpio3
spi_software_miso_pin: PITB:gpio4
cs_pin: PITB:gpio1
interpolate: True
#diag0_pin: PITB:gpio7
run_current: 0.800 
hold_current: 0.500
##stealthchop_threshold: 0

[stepper_y]
##	Connected to MOT1 (A Motor)
step_pin: PITB:gpio13
dir_pin: PITB:gpio23
enable_pin: !PITB:gpio22
rotation_distance: 40
microsteps: 16
full_steps_per_rotation:200  #set to 400 for 0.9 degree stepper
endstop_pin: ^PITB:gpio17
position_min: 0
##--------------------------------------------------------------------

##	Uncomment for 250mm build
#position_endstop: 250
#position_max: 250

##	Uncomment for 300mm build
position_endstop: 305
position_max: 305

##	Uncomment for 350mm build
#position_endstop: 350
#position_max: 350

##--------------------------------------------------------------------
homing_speed: 25  #Max 100
homing_retract_dist: 5
homing_positive_dir: true

##  Make sure to update below for your relevant driver (5160)
[tmc5160 stepper_y] 
# Soft SPI
spi_software_sclk_pin: PITB:gpio2
spi_software_mosi_pin: PITB:gpio3
spi_software_miso_pin: PITB:gpio4
cs_pin: PITB:gpio10
#diag0_pin: PITB:^gpio14
interpolate: True 
run_current: 0.8
hold_current: 0.5
##stealthchop_threshold: 0

# You will need to configure a neopixel (or other addressable led, such as dotstar). See
# https://www.klipper3d.org/Config_Reference.html#neopixel for configuration details.
# And you can get sb led MACRO here: https://github.com/PrinterConfigs/DoomConfig/blob/master/stealthburner.cfg
# Or here https://github.com/sttts/voron-klipper-config/blob/master/stealthburner_leds.cfg
[neopixel leds]
pin: PITB:gpio19
chain_count: 3
color_order: GRBW
initial_RED: 0.5
initial_GREEN: 0.5
initial_BLUE: 0.5
initial_WHITE: 0.5

[fan_generic fg1]
# FAN0
pin: PITB:gpio0

[fan_generic fg2]
# FAN1
pin: PITB:gpio18

[temperature_sensor chamber]
# T0 GPIO26
# T1 GPIO27
# T2 GPIO28
sensor_type: Generic 3950
sensor_pin: PITB:gpio26
min_temp: 0
max_temp: 100
gcode_id: C

[output_pin activity_led]
pin: PITB:gpio15

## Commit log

2023-01-14 Upload PITB pinout and klipper cfg
    [pitb.cfg]
2024-06-12 upload 2.0
    [pitb.cfg]
2024-09-04 fix v2
    [pitbv2.cfg]
